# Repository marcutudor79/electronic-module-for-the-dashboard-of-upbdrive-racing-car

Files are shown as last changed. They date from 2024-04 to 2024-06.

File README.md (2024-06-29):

# ETTI-Bachelor's degree Applied Electronics


My Bachelor's degree that consists in research & design the following components:
- dashboard PCB with ESP32 SoC
- Test module PCB with Raspberry Pi Pico devboard
- Firmware for the ESP32 with ESP-IDF
- Firmware for the Raspberry Pi Pico with pico-sdk

# Thesis
The document can be referred [here.](Documentation/Thesis.pdf)

# Thesis summary
The thesis sumarry can be referred [here.](Documentation/Summary.pdf)

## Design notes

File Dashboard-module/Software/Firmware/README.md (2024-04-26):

# Firmware documentation

## Project structure:
```
- Firmware /
            - CMakeLists.txt /* project wide CMake */

            - components/ - 4dsystems-project/ - 4dsys.4dGenie /* the project from 4D
                                                                  Workshop IDE */
                          - esp32-arduino /* the arduino interface for ESP, used for
                                             compatibility between visi-genie and the
                                             ESP-IDF build system */
                          - visi-genie /* the interface for display communication */

            - main/       - CMakeLists.txt /* main CMakeLists, used to include the main.c */
                          - main.cpp       /* the main file of the project */

            - misc/         /* photos included in the README.md file */

            - README.md     /* project README file */
```

# How to run this project:
Install the SDK:
1. Go to VS Code tutorial for ESP-IDF extension from [here](https://github.com/espressif/vscode-esp-idf-extension/blob/master/docs/tutorial/install.md)
2. Install the ESP-IDF using the "EXPRESS" setup
3. The project was made by using the release version 5.1.1

Install the 4DSystems IDE:
1. Go to the 4DSystems website from [here](https://4dsystems.com.au/software/)
2. Download the free version of Workshop4 IDE
3. Open the file components/4dsystems-project/4dsys.4DGenie with Workshop4 IDE
4. Extract the SDCard from the display and connect it to your computer
5. Click on the project tab and set the Destination, Initial Form, Comms Speed, Comms and File System as in the picture below



6. Click on the home tab and then click on the Build (Copy/Load) button
7. A window will pop up, there you need to select the drive, that being the SDCard
from the display

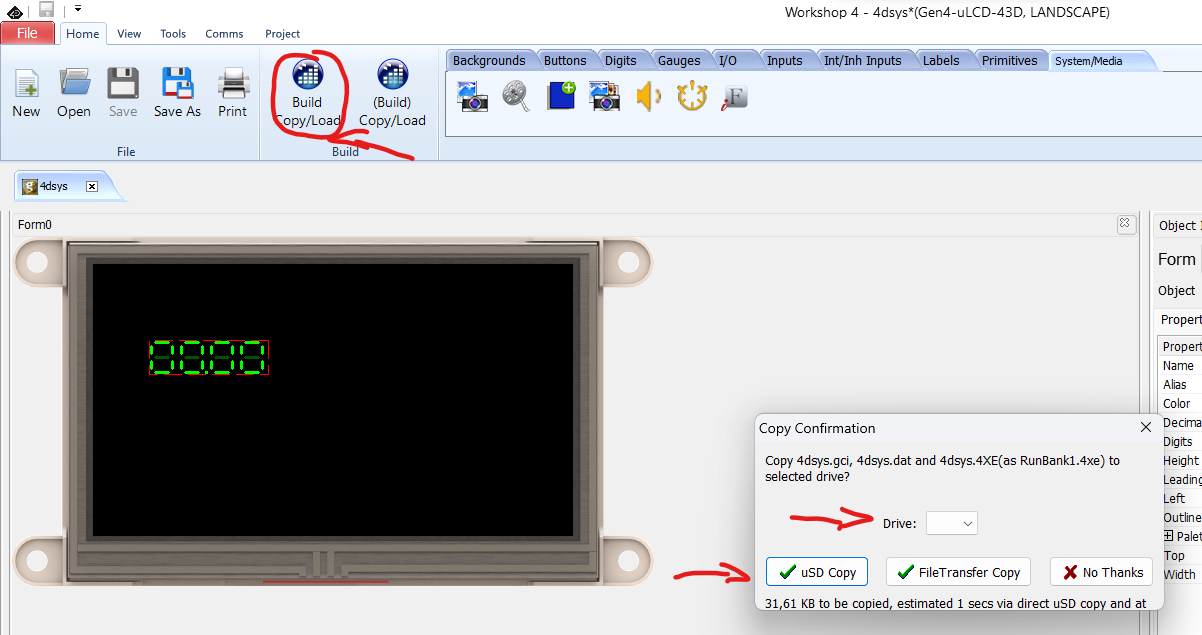
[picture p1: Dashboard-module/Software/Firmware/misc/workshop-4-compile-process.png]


8. Then select uSD Copy
9. After that, pop the SDCard back inside the screen
10. After a power cycle, it will prompt the message "flashing complete"
11. Now the display programming is complete

Run the project:
1. Open this directory "Firmware" in VS Code
2. Build the project by using ESP-IDF Build Project button
3. Select the COM port to your board
4. Flash the project by using UART
5. Enjoy the endless loop of numbers incrementing on the screen!

Schematic:
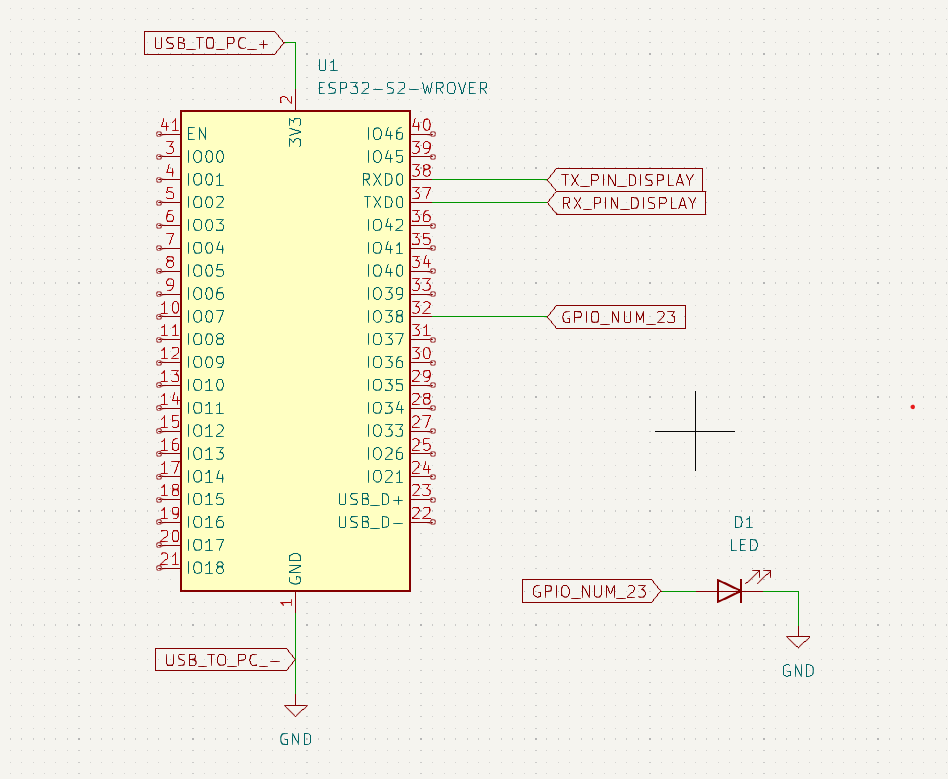
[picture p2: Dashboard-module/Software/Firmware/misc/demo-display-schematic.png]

NOTE: You will also need a 5V power supply in order to power up the display.

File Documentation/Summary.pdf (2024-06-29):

Study program: Applied Electronics (ETC-ELAeng), 2024

### Electronic Module for the Dashboard of a Formula Student Racing Car

Project objectives: The student must build from scratch an electronic module that will act as an interface between the pilot and the Formula Student race car it. The module will monitor the CAN bus of the car, from which it takes the following data points: oil temperature and water temperature, the status of the hybrid system as well as real-time data such: RPM and the current gear. It will also include an accelerometer on the same PCB. All the sampled data will be shown on an LCD module as well as a web interface which will be served by the HTTP server of the ESP32 microcontroller. The PCB will integrate an SD card that stores the data points in a file, which can be downloaded via the web interface.
A test module will be implemented on a second PCB for the student to showcase the functionality of the dashboard electronic module. It emulates the ECU of the Formula Student race car and will send via CAN the above-mentioned data. This module will feature the Raspberry Pi Pico microcontroller.
From a hardware perspective, the following components will be used:
- ESP32 WROOM 32 microcontroller as the brains of the dashboard electronic module
- SN65HVD230D CAN Transceiver that will act as an interface between ESP32 and the CAN bus
- LCD module from 4DSystems to show the data in a graphical interface to the pilot
- NeoPixel Stick - 8 x 5050 RGB LED that will be the shift bar, which signals the right moment to change the gear
- Panel mount buttons which will be the way of interacting with the dashboard module Project fulfilment and results: To fulfill the above-mentioned requirements, PCB Design as well as advanced C/C++ programming techniques had to be used. The contributions for this project are not trivial, since the PCB of the dashboard had to be designed from scratch, as well as the PCB of the testing module. No development boards were used on the dashboard module. It has a schematic that integrates all the needed peripherals as well as the ESP32 SoC with its necessary programming peripherals. To achieve this, the schematic of the ESP32 WROOM 32 dev board was analyzed and reimplemented in the KiCAD EDA.
Besides this, the dashboard includes standalone power delivery circuitry, which includes a LDO regulator, that converts the 5V power rail into a 3V3 power rail which is used for the ESP32, SD card module, CP2102 programming chip, the Hybrid selector, and the CAN transceiver SN65HVD230DR. The 5V rail is converted from the 12V power rail of the Formula Student racing car, by a buck converter. The circuit of the buck includes the components used in the reference design, given by its datasheet, for a 5V 3A output.
Other circuitry that needed to be implemented on the PCB were the MPU6050 accelerometer circuitry and the I2C lines that go to the ESP32 SoC, the SD card circuitry with all the necessary pull-up resistors as well as filtering for the 3V3 rail via ceramic capacitors of 1uF and 0.1uF. A lot of capacitors are used for filtering in the dashboard schematic to remove the noise induced by the buck. As a fail-over technique, the 3V3 rail can be supplied also by the LCD, which includes an LDO itself. This is achieved by placing on the PCB a solder jumper.
The LCD connector is a 30-pin ribbon cable connector. The pins of this connector were used as per the specification sheet of the 4DSystems company. Therefore, multiple LCD screens can be used with the same PCB as they all respect the same pinout of the ribbon connector.
The PCB is a 2 layer one, components being installed mostly on the front copper layer, the only exceptions being the LDO, because of its large footprint, and the automotive harness connector of the dashboard module, which needs to be oriented to the back of the PCB.

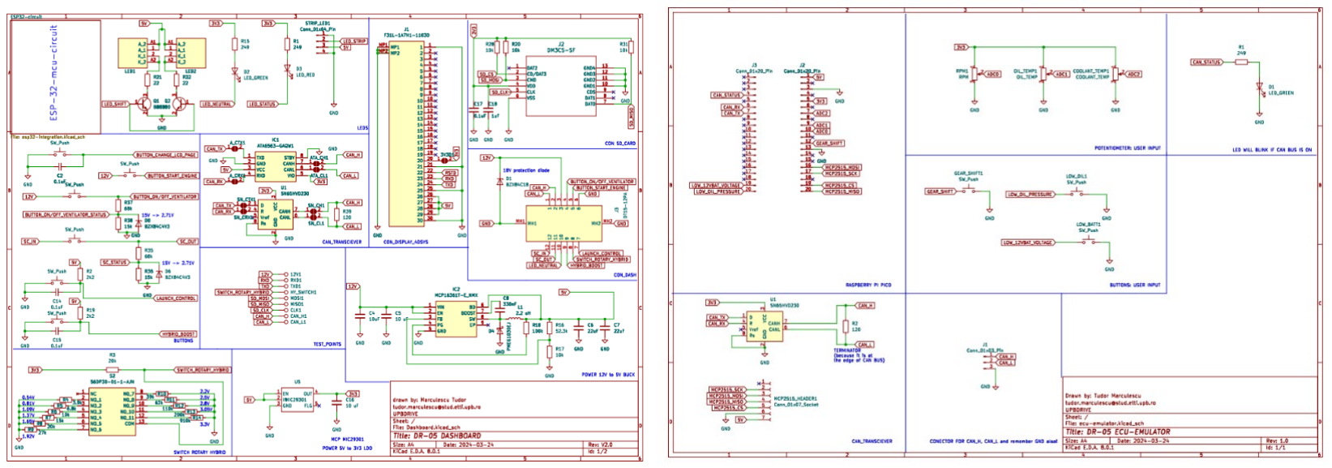
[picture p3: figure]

Fig. 1 Schematics of the dashboard module and test module
The PCB design of the test module is also based on a 2-layer approach, this time by using the PCB as an interconnection method between the Raspberry Pi Pico development board and the MCP2515 development board from Microchip, which includes a CAN controller that communicates via SPI with the Pico.
The PCB features 3 potentiometers that are used to emulate the RPM, water temperature and oil temperature signals from the ECU (Electronic Control Module), as well as 3 buttons that emulate a gear change, low oil pressure signal and low battery voltage signal. The low oil and low battery signals are used to showcase the function of the dashboard to display error messages on the LCD, in order to inform the pilot in case of catastrophic failures. The dashboard module and the test module will be connected via the CAN bus lines: CAN HIGH and CAN LOW, through which the test module will send CAN packets with the data acquired from the potentiometers and the buttons.

Do not think that this data is not converted into actual RPM and temperature values! Pico does all the data conversion in its firmware then formats the data into CAN packets which are send via the bus by the MCP2515 CAN controller.

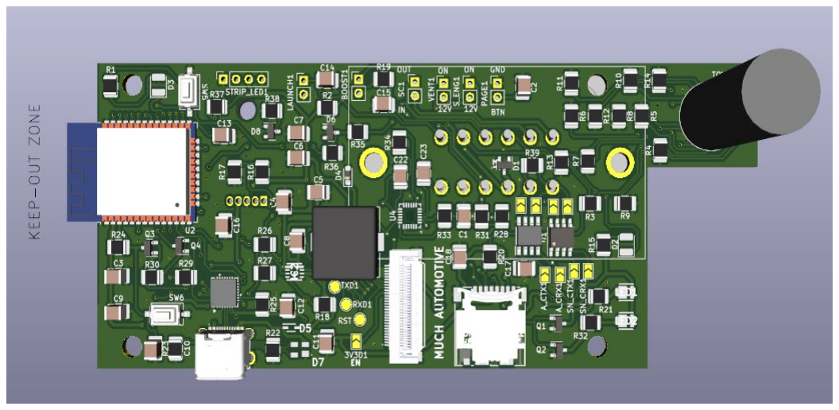
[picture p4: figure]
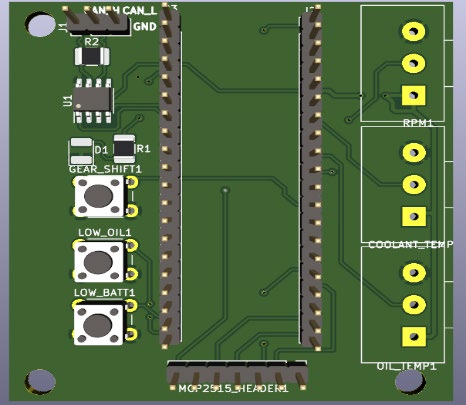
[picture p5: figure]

Fig. 2 3D View of the dashboard and test module
From a software point of view, the ESP32 one is complex, since it integrates a RTOS (Real Time Operating System). This allows the firmware to run on multiple threads on the same core of the microcontroller, and to also run parts of the firmware in parallel, by using multicore processing. In this way, CAN read and send tasks and LCD communication task, which are considered high priority, can be run completely parallel on 2 cores of the ESP32.
To achieve the highest performance possible, ESP32 was clocked to 240Mhz, which is the maximum supported by its Tensilica xTensa cores. Please note that this module is powered by a combustion engine, therefore efficiency is not considered, since it’s already lost in combustion. Espressif, the company which designed the ESP32 microcontroller, offers an IDF (Integrated Development Framework), written in C programming language, that includes a special flavor of FreeRTOS. It was adapted to run precisely on the hardware of Espressif. FreeRTOS is a renowned software solution for real-time applications in the automotive industry. If one uses this RTOS, he needs to break the code into multiple functions, which are called tasks.
Tasks are one of the most important concept of RTOS. They have different priorities, therefore when a high priority task is scheduled to be executed, it will preempt the lower priority ones. This allows the programmer to have certainty that high priority code will always be executed as scheduled by him. However, if no higher priority tasks need to be executed, lower priority ones are put into execution, therefore achieving the principle of multiple thread processing, since on one core, not only the high priority task is executed, assuming it will have some idle time, but also the lower priority ones. Multiple tasks had to be developed in order to achieve all the features proposed: accelerometer read task via I2C bus, SD card write task via SPI and VFS (Virtual File System) library, LCD communication task via UART2 IP, the HTTP server backend, etc. The html web interface was embedded in the binary that is flashed on the ESP32, therefore only the log file is stored on the SD card, not the index.html and its additional files used on the web interface.

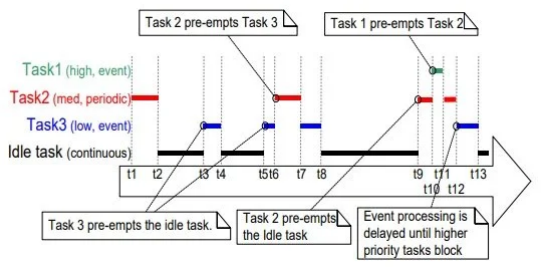
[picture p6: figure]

Fig. 3 Preemptive scheduling
To communicate with the NeoPixel LED bar, NRZ (Non-Return to Zero) protocol was used. The protocol was emulated with the RMT (ReMoTe control) library of the ESP32. The RMT is usually used to emulate TV remote control signals on the microcontroller’s pins, however, it can be also integrated to respect the protocol used by all 8 LEDs of the shift bar, which communicate with the ESP32 only via 1 pin. Data sharing between cores and threads is done using Semaphores which are a way of excluding race conditions on the same memory location.
Raspberry Pi Pico was programmed using bare metal programming techniques in C++. It does not include any operating system, and only runs one thread of monolithic code. This proves to be problematic, in case the code will get as complex as the dashboard firmware, but for the test board use case, it’s more than reasonable to not use RTOS. The main features are ADC reading of multiple potentiometers via ADC pins on the Pico development board and button state polling, the formatting of CAN packets. The packets are objects in C++, defined by a library developed for the MCP2515. In the dashboard firmware a common C data structure was used to store the display data, which is also integrated into the Pico C++ firmware to make the codebase more uniform and easier to understand. The CAN packet identifiers are also uniform between the dashboard and test module firmware as well as the packet formatting functions.

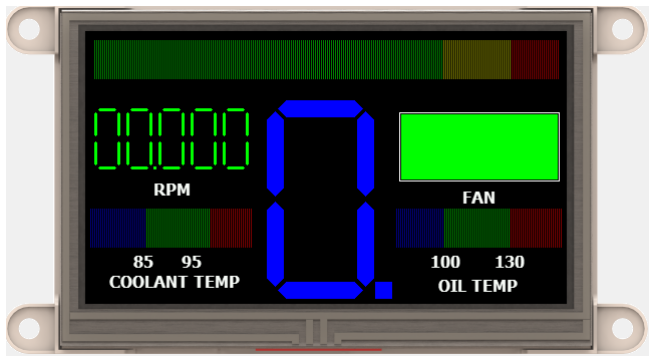
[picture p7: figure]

Fig. 4 Pilot interface
The dashboard was tested in an empiric method by trying all its functionalities and running it over an extended period. No crashes were detected during the test run time, therefore, it can be said that all the proposed student contributions were achieved, and the project development was a success.

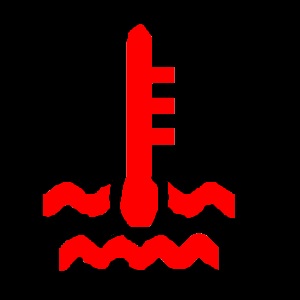
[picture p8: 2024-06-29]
Dashboard-module/Software/Firmware/4dsystems-project/high-water-temp.jpg

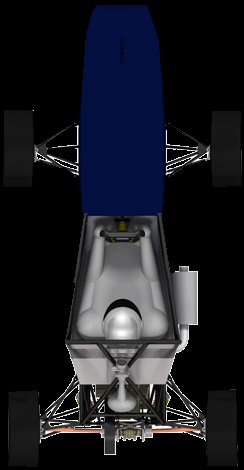
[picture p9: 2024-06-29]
Dashboard-module/Software/Firmware/4dsystems-project/4dsys.ImgData/car-tyrepressure.jpg

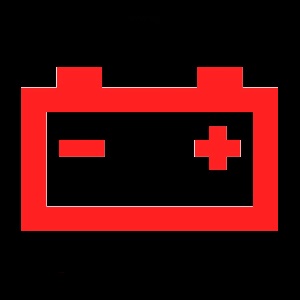
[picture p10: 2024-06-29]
Dashboard-module/Software/Firmware/4dsystems-project/low-battery.jpg

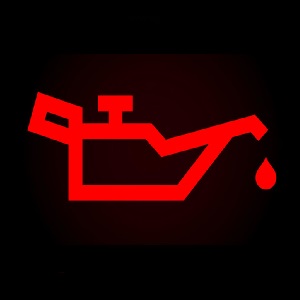
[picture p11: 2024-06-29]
Dashboard-module/Software/Firmware/4dsystems-project/4dsys.ImgData/low-oil-pressure.jpg

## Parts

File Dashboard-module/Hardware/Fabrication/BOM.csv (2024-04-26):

Reference | Value | Mouser Price/Stock | Qty
3V3 | TestPoint |  | 1
3V3D1 | SolderJumper_2_Open |  | 1
12V1 | TestPoint |  | 1
ATA_CH1 | SolderJumper_2_Open |  | 1
ATA_CL1 | SolderJumper_2_Open |  | 1
A_CRX1 | SolderJumper_2_Open |  | 1
A_CTX1 | SolderJumper_2_Open |  | 1
BOOST1 | SW_Push |  | 1
BOOT1 | TestPoint |  | 1
C1, C2, C9, C10, C12-C15, C17, C23 | 0.1uF | https://ro.mouser.com/ProductDetail/KEMET/C1210C104K5RACAUTO?qs=6HsNZxDn%2FfKYeoMwfZiUQw%3D%3D | 10
C3, C6, C7 | 22uF | https://www.mouser.co.uk/ProductDetail/Samsung-Electro-Mechanics/CL32B226KAJNNNE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 | 3
C4 | 10uF | https://www.mouser.co.uk/ProductDetail/Samsung-Electro-Mechanics/CL32B106KBJNNNE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 | 1
C5, C16 | 10 uF | https://www.mouser.co.uk/ProductDetail/Samsung-Electro-Mechanics/CL32B106KBJNNNE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 | 2
C8 | 330nF | https://ro.mouser.com/ProductDetail/KEMET/C1210C334J3RACTU?qs=6mECUfS0Ke6nQoOxT4SD9w%3D%3D | 1
C11, C18 | 1uF | https://ro.mouser.com/ProductDetail/KEMET/C1210C105K5RACAUTO?qs=6HsNZxDn%2FfKtobC7oxYdSw%3D%3D | 2
C22 | 2.2nF | https://ro.mouser.com/ProductDetail/KEMET/C1210C222KGRACAUTO?qs=YCa%2FAAYMW00YYMxRYUmDPg%3D%3D | 1
CAN_H1 | TestPoint |  | 1
CAN_L1 | TestPoint |  | 1
CLK1 | TestPoint |  | 1
D1 | BZX84C18 | https://eu.mouser.com/ProductDetail/Diotec-Semiconductor/BZX84C18?qs=OlC7AqGiEDmBdo82ioIQJw%3D%3D | 1
D2 | LED_GREEN | https://www.mouser.co.uk/ProductDetail/Broadcom-Avago/ASMT-BG20-AS000?qs=ZNK0BnemlqFrc3sIHSfGyw%3D%3D | 1
D3 | LED_RED | https://www.mouser.co.uk/ProductDetail/Broadcom-Avago/ASMT-BR20-AS000?qs=ZNK0BnemlqE0pAy34cXyOA%3D%3D | 1
D4 | PMEG1030EJ | https:/ro.mouser.com/ProductDetail/Nexperia/PMEG1030EJ115?qs=LOCUfHb8d9vmk7P%2FuYbs5A%3D%3D | 1
D5 | BAT760-7 | https://www.mouser.co.uk/ProductDetail/Diodes-Incorporated/BAT760-7?qs=JV7lzlMm3yKDDyO09xoRbQ%3D%3D | 1
D6, D8 | BZX84C4V3 | https://eu.mouser.com/ProductDetail/Diotec-Semiconductor/BZX84C18?qs=OlC7AqGiEDmBdo82ioIQJw%3D%3D | 2
D7 | SP0503BAHTG | https://www.mouser.co.uk/ProductDetail/Littelfuse/SP0503BAHTG?qs=uD%2FdkN7XIa0NTYXwHdELYA%3D%3D | 1
EN1 | TestPoint |  | 1
GND1 | TestPoint |  | 1
HY_SWITCH1 | TestPoint |  | 1
IC1 | ATA6563-GAQW1 | https://www.mouser.co.uk/ProductDetail/Microchip-Technology/ATA6563-GAQW1?qs=byeeYqUIh0Or75RXPLSWhg%3D%3D | 1
IC2 | MCP16361T-E_NMX | https://www.mouser.co.uk/ProductDetail/Microchip-Technology/MCP16361T-E-NMX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 | 1
J1 | F31L-1A7H1-11030 | https://www.mouser.co.uk/ProductDetail/Amphenol-Aorora/F31L-1A7H1-11030?qs=xZ%2FP%252Ba9zWqba3JhFjnTbQA%3D%3D | 1
J2 | DM3CS-SF | https://eu.mouser.com/ProductDetail/Hirose-Connector/DM3CS-SF?qs=tTj%252BmQ3KZwbB9K5zh89Rcw%3D%3D | 1
J3 | DT15-12PA | https://www.mouser.co.uk/ProductDetail/TE-Connectivity-DEUTSCH/DT15-12PA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 | 1
J6 | USB4800-03-A | https://www.mouser.co.uk/ProductDetail/GCT/USB4800-03-A?qs=vvQtp7zwQdMkfG8vViEZoQ%3D%3D | 1
L1 | 2.2 uH | https://www.mouser.co.uk/ProductDetail/Vishay-Dale/IHLP5050CEER2R2M01?qs=rJUnqL1uSaJB3797G0edMw%3D%3D | 1
LAUNCH1 | SW_Push |  | 1
LED1, LED2 | GR_PSLM31.23-FTGP-45-FG | https://www.mouser.co.uk/ProductDetail/OSRAM-Opto-Semiconductors/GR-PSLM3123-FTGP-45-FG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 | 2
MISO1 | TestPoint |  | 1
MOSI1 | TestPoint |  | 1
PAGE1 | SW_Push |  | 1
Q1-Q4 | BC850 | https://www.mouser.co.uk/ProductDetail/Infineon-Technologies/BC-850B-E6327?qs=OWKQh20churjjEOHOyP6%2FA%3D%3D | 4
R1, R15 | 249 | https://www.mouser.co.uk/ProductDetail/YAGEO/AC1210FR-07249RL?qs=9h0bZHM%2F3zLfUZmwuLVpmw%3D%3D | 2
R2, R19 | 2k2 | https://www.mouser.co.uk/ProductDetail/YAGEO/RC1210JR-072K2L?qs=6sj9KdP9svikZPTMueIMVw%3D%3D | 2
R3, R8 | 20k | https://www.mouser.co.uk/c/passive-components/resistors/film-resistors/thick-film-resistors-smd/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 | 2
R4 | 3.9k | https://www.mouser.co.uk/ProductDetail/YAGEO/AC1210FR-073K9L | 1
R5 | 6.8k | https://www.mouser.co.uk/ProductDetail/YAGEO/AC1210JR-076K8L?qs=tggtontpCXOplOrJrmjEFg%3D%3D | 1
R6, R17, R20, R28, R31 | 10k | -- mixed values -- | 5
R7, R36, R38 | 15k | -- mixed values -- | 3
R9 | 27k | https://www.mouser.co.uk/ProductDetail/YAGEO/RC1210JR-0727KL?qs=6sj9KdP9svjllLJjfo7WyQ%3D%3D | 1
R10 | 39k | https://www.mouser.co.uk/ProductDetail/YAGEO/AC1210FR-0739KL?qs=tggtontpCXMMf8qT%2FAbRXA%3D%3D | 1
R11 | 62k | https://www.mouser.co.uk/ProductDetail/YAGEO/RC1210FR-0762KL?qs=H6bTqIa4pvXpTu6n%252B%2FNlGA%3D%3D | 1
R12 | 110k | https://www.mouser.co.uk/ProductDetail/YAGEO/RC1210FR-07110KL?qs=H6bTqIa4pvVTUx5WugF8mg%3D%3D | 1
R13 | 200k | https://www.mouser.co.uk/ProductDetail/YAGEO/RC1210JR-07200KL?qs=CteSnpDdeuDthvIZoegoUw%3D%3D | 1
R14 | 910k | https://www.mouser.co.uk/c/passive-components/resistors/film-resistors/thick-film-resistors-smd/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 | 1
R16 | 52.3k | https://ro.mouser.com/ProductDetail/Panasonic/ERJ-14NF5232U?qs=nho8PGNfA6qGgoBnQlUYNQ%3D%3D | 1
R18 | 100k | https://ro.mouser.com/c/?q=RC1210FR-07100KL | 1
R21, R32 | 22 | https://www.mouser.co.uk/ProductDetail/YAGEO/AC1210JR-0722RL?qs=9h0bZHM%2F3zJh6BccmgJFgA%3D%3D | 2
R22, R23 | 5.1k | https://www.mouser.co.uk/ProductDetail/YAGEO/RC1210FR-075K1L?qs=H6bTqIa4pvX6KFbI5%252BKNQQ%3D%3D | 2
R24, R25, R29, R30 | 10K | https://ro.mouser.com/ProductDetail/SEI-Stackpole/RMCF1210FT10K0?qs=FESYatJ8odLSM832du%2FSXw%3D%3D | 4
R26 | 22.1k | https://ro.mouser.com/ProductDetail/Vishay-Dale/CRCW121022K1FKEA?qs=grCzdrupEeFjmAghhFVXQQ%3D%3D | 1
R27 | 47.5k | https://ro.mouser.com/ProductDetail/Vishay-Dale/CRCW121047K5FKEA | 1
R33, R34 | 1.5k | https://www.mouser.co.uk/ProductDetail/YAGEO/RC1210JR-071K5L?qs=6sj9KdP9sviSuJXf5F9TBg%3D%3D | 2
R35, R37 | 68k | -- mixed values -- | 2
R39 | 120 | https://www.mouser.co.uk/ProductDetail/YAGEO/RC1210JR-13120RL?qs=qpJ%252B%252B%252Bdg6p3wDlUWdPJ5VQ%3D%3D | 1
RXD0, RXD1 | TestPoint |  | 2
S2 | 56DP30-01-1-AJN | https://www.mouser.co.uk/ProductDetail/Grayhill/56DP30-01-1-AJN?qs=ls7QRyWmRk4hkEWp7Raugg%3D%3D | 1
SC1 | SW_Push |  | 1
SCL1 | TestPoint |  | 1
SDA1 | TestPoint |  | 1
SN_CH1 | SolderJumper_2_Open |  | 1
SN_CL1 | SolderJumper_2_Open |  | 1
SN_CRX1 | SolderJumper_2_Open |  | 1
SN_CTX1 | SolderJumper_2_Open |  | 1
STRIP_LED1 | Conn_01x04_Pin | https://www.mouser.co.uk/ProductDetail/Harwin/M20-9992046?qs=%252Bk6%2F5FB6qrkVgm0dNoxueg%3D%3D | 1
SW5, SW6 | boot_button | https://ro.mouser.com/ProductDetail/CK/PTS636-SK25-SMTR-LFS?qs=vLWxofP3U2wQKecmu1U%2FMA%3D%3D | 2
S_ENG1 | SW_Push |  | 1
TXD0, TXD1 | TestPoint |  | 2
U1 | SN65HVD230 | https://eu.mouser.com/ProductDetail/Texas-Instruments/SN65HVD230DR?qs=QViXGNcIEAtifeQR3pYVUQ%3D%3D | 1
U2 | ESP32-WROOM-32 | https://ro.mouser.com/ProductDetail/Espressif-Systems/ESP32-WROOM-32E-H4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 | 1
U3 | CP2102-GMR | https://ro.mouser.com/ProductDetail/Silicon-Labs/CP2102-GMR?qs=cNyzPCcHMUWu%2FiPhR8KQAw%3D%3D | 1
U4 | MPU-6050 | https://www.mouser.co.uk/ProductDetail/TDK-InvenSense/MPU-6050?qs=u4fy%2FsgLU9O14B5JgyQFvg%3D%3D | 1
U5 | MIC29301 |  | 1
VENT1 | SW_Push |  | 1

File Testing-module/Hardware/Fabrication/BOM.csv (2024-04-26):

Reference | Value | Mouser Price/Stock | Qty
COOLANT_TEMP1 | COOLANT_TEMP | https://eu.mouser.com/ProductDetail/CUI-Devices/PTN16-A50115K1B1?qs=VJzv269c%252BPYgMEvZAio5MQ%3D%3D | 1
D1 | LED_GREEN | https://www.mouser.co.uk/ProductDetail/Broadcom-Avago/ASMT-BG20-AS000?qs=ZNK0BnemlqFrc3sIHSfGyw%3D%3D | 1
GEAR_SHIFT1 | SW_Push | https://eu.mouser.com/ProductDetail/CUI-Devices/TS02-66-73-BK-160-LCR-D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 | 1
J1 | Conn_01x03_Pin | https://www.mouser.co.uk/ProductDetail/Harwin/M20-9992046?qs=%252Bk6%2F5FB6qrkVgm0dNoxueg%3D%3D | 1
J2, J3 | Conn_01x20_Pin | https://www.mouser.co.uk/ProductDetail/Harwin/M20-9992046?qs=%252Bk6%2F5FB6qrkVgm0dNoxueg%3D%3D | 2
LOW_BATT1 | SW_Push | https://eu.mouser.com/ProductDetail/CUI-Devices/TS02-66-73-BK-160-LCR-D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 | 1
LOW_OIL1 | SW_Push | https://eu.mouser.com/ProductDetail/CUI-Devices/TS02-66-73-BK-160-LCR-D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 | 1
MCP2515_HEADER1 | Conn_01x07_Socket | https://www.mouser.co.uk/ProductDetail/Harwin/M20-9992046?qs=%252Bk6%2F5FB6qrkVgm0dNoxueg%3D%3D | 1
OIL_TEMP1 | OIL_TEMP | https://eu.mouser.com/ProductDetail/CUI-Devices/PTN16-A50115K1B1?qs=VJzv269c%252BPYgMEvZAio5MQ%3D%3D | 1
R1 | 249 | https://www.mouser.co.uk/ProductDetail/YAGEO/AC1210FR-07249RL?qs=9h0bZHM%2F3zLfUZmwuLVpmw%3D%3D | 1
R2 | 120 | https://www.mouser.co.uk/ProductDetail/YAGEO/RC1210JR-13120RL?qs=qpJ%252B%252B%252Bdg6p3wDlUWdPJ5VQ%3D%3D | 1
RPM1 | RPM | https://eu.mouser.com/ProductDetail/CUI-Devices/PTN16-A50115K1B1?qs=VJzv269c%252BPYgMEvZAio5MQ%3D%3D | 1
U1 | SN65HVD230 | https://eu.mouser.com/ProductDetail/Texas-Instruments/SN65HVD230DR?qs=QViXGNcIEAtifeQR3pYVUQ%3D%3D | 1

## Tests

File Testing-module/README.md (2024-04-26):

# ECU Emulator

## Description
In order to debug the CAN bus as well as the dashboard module, this ECU Emulator
injects CAN packets into the CAN bus. It is a replacement for the ECU itself, because
we cannot use it just for electronics debugging, it has to be mounted in the FS car.

## How does it work
This ECU Emulator uses a potentiometer to emulate the accelerator pedal of the FS car
as well as a button to emulate the gear shift. The potentiometer is read via the built-in
ADC module of the Raspberry Pi Pico board, and the button is read using GPIO functions.

### How is the data generated
- rpm is generated using a constant 800 + the potentiometer value + a random number
between 0 - 49 in order to emulate the actual rpm of the FS car. The expected range is
between 800 - 13000.
- current gear is initially 0 (netural) and incremented when the button is pressed, until 4,
then it is set back to 0.
- all the other data is assigned the saw tooth signal between 0 - 250.

The CAN packets are formatted with respect to the CAN Packet allocation excel and then sent via the CAN bus.

## Project structure
```
- Docs     /* folder the documentation files */
- Firmware /
            - components/ - adc                 /* part of the code that enables the onboard
                                                    adc and configures a gpio to read a button */
                          - can                 /* part of the code that enables can communication
                                                    via the can bus transciever
                                                    also formats the packets according to the CAN
                                                    packet allocation */
                          - common              /* contains a header file in which the pins used
                                                    in the project are defined */
                          - heartbeat           /* part of the code that enables the built-in LED
                                                    to blink, for debug purposes */
                          - signal-generation   /* part of the code that generates the rpm data,
                                                   CurrentGear data and a sawtooth signal that
                                                   will replace the other data in the CAN packets */
            - main                /* contains the main source and header file with
                                    which describes the main loop of the program */
            - modules             /* contains can2040 git submodule that enables
                                     the PICO to communicate via CAN using bit banging
                                     on GPIOs */

- README.md /* project README file */
```

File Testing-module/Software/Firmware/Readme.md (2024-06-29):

# ECU Emulator Firmware

## How to build the project (on Windows)
1. Open a console (cmd) with the path set to 'Firmware' directory

2. Change directory into the 'main' folder

    ```
    cd main
    ```

3. Create a build directory

    ```
    mkdir build
    cd build
    ```

4. Use 'cmake' to generate the build files
    ```
    cmake ..
    ```

5. Build the project using 'cmake'
    ```
    cmake --build .
    ```

6. Copy main.uf2 file on the Raspberry Pi Pico board

## Prerequisites (on Windows)

Follow this tutorial [https://shawnhymel.com/2096/how-to-set-up-raspberry-pi-pico-c-c-toolchain-on-windows-with-vs-code/.](https://shawnhymel.com/2096/how-to-set-up-raspberry-pi-pico-c-c-toolchain-on-windows-with-vs-code/)

! 'Download Pico SDK and Examples' part is not needed for this project

! 'Install VS Code' part is not needed for this project

! 'Build Blink Example' part is needed for this project

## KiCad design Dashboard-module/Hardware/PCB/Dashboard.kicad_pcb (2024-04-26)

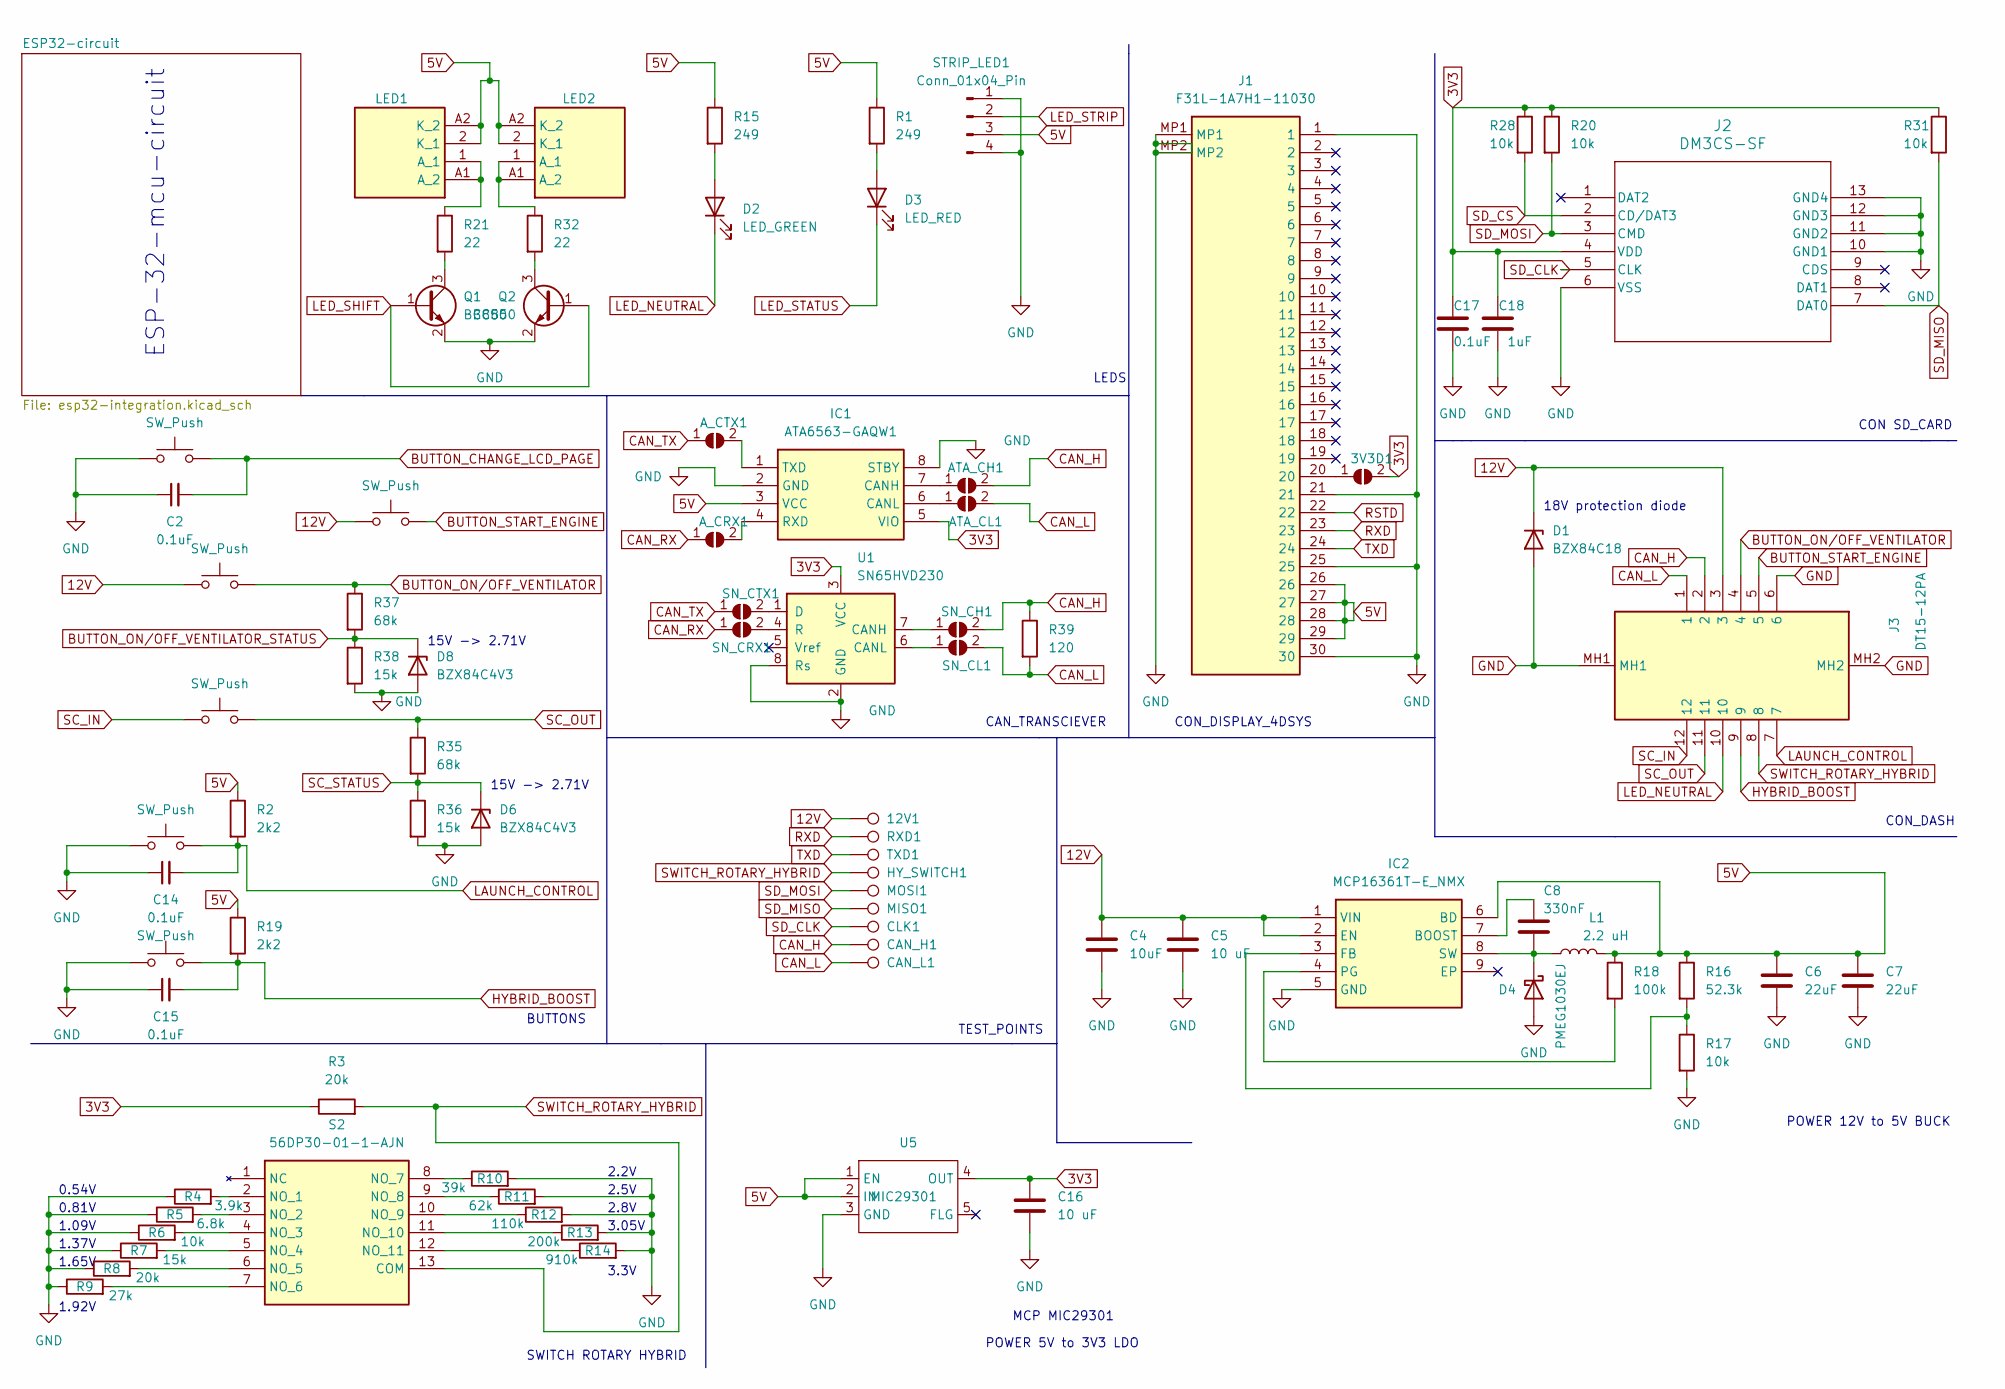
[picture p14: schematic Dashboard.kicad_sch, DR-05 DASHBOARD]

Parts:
3V3D1: SolderJumper_2_Open; SolderJumper-2_P1.3mm_Open_TrianglePad1.0x1.5mm
12V1: TestPoint; TestPoint_Pad_D2.0mm
ATA_CH1: SolderJumper_2_Open; SolderJumper-2_P1.3mm_Open_TrianglePad1.0x1.5mm
ATA_CL1: SolderJumper_2_Open; SolderJumper-2_P1.3mm_Open_TrianglePad1.0x1.5mm
A_CRX1: SolderJumper_2_Open; SolderJumper-2_P1.3mm_Open_TrianglePad1.0x1.5mm
A_CTX1: SolderJumper_2_Open; SolderJumper-2_P1.3mm_Open_TrianglePad1.0x1.5mm
BOOST1: SW_Push; PinHeader_1x02_P2.54mm_Vertical
C2, C14, C15, C17: 0.1uF; C_1210_3225Metric_Pad1.33x2.70mm_HandSolder
C4: 10uF; C_1210_3225Metric_Pad1.33x2.70mm_HandSolder
C5, C16: 10 uF; C_1210_3225Metric_Pad1.33x2.70mm_HandSolder
C6, C7: 22uF; C_1210_3225Metric_Pad1.33x2.70mm_HandSolder
C8: 330nF; C_1210_3225Metric_Pad1.33x2.70mm_HandSolder
C18: 1uF; C_1210_3225Metric_Pad1.33x2.70mm_HandSolder
CAN_H1: TestPoint; TestPoint_Pad_D2.0mm
CAN_L1: TestPoint; TestPoint_Pad_D2.0mm
CLK1: TestPoint; TestPoint_Pad_D2.0mm
D1: BZX84C18; SOT-23
D2: LED_GREEN; D_1210_3225Metric
D3: LED_RED; D_1210_3225Metric
D4: PMEG1030EJ; D_SOD-323_HandSoldering
D6, D8: BZX84C4V3; SOT-23
HY_SWITCH1: TestPoint; TestPoint_Pad_D2.0mm
IC1: ATA6563-GAQW1; SOIC127P600X175-8N; Mouser Part Number 579-ATA6563-GAQW1
IC2: MCP16361T-E_NMX; MCP16361TENMX; Mouser Part Number 579-MCP16361T-E/NMX
J1: F31L-1A7H1-11030; F31L1A7H111030; Mouser Part Number 649-F31L-1A7H1-11030
J2: DM3CS-SF; DM3CS_SF
J3: DT15-12PA; DT1512PA; Mouser Part Number 571-DT15-12PA
L1: 2.2 uH; L_Vishay_IHLP-5050
LAUNCH1: SW_Push; PinHeader_1x02_P2.54mm_Vertical
LED1, LED2: GR_PSLM31.23-FTGP-45-FG; GRPSLM3123FTGP45FG; Mouser Part Number 720-PSLM3123A4675
MISO1: TestPoint; TestPoint_Pad_D2.0mm
MOSI1: TestPoint; TestPoint_Pad_D2.0mm
PAGE1: SW_Push; PinHeader_1x02_P2.54mm_Vertical
Q1, Q2: BC850; SOT-23
R1, R15: 249; R_1210_3225Metric
R2, R19: 2k2; R_1210_3225Metric
R3, R8: 20k; R_1210_3225Metric_Pad1.30x2.65mm_HandSolder
R4: 3.9k; R_1210_3225Metric_Pad1.30x2.65mm_HandSolder
R5: 6.8k; R_1210_3225Metric_Pad1.30x2.65mm_HandSolder
R6, R17, R20, R28, R31: 10k; R_1210_3225Metric_Pad1.30x2.65mm_HandSolder
R7: 15k; R_1210_3225Metric_Pad1.30x2.65mm_HandSolder
R9: 27k; R_1210_3225Metric_Pad1.30x2.65mm_HandSolder
R10: 39k; R_1210_3225Metric_Pad1.30x2.65mm_HandSolder
R11: 62k; R_1210_3225Metric_Pad1.30x2.65mm_HandSolder
R12: 110k; R_1210_3225Metric_Pad1.30x2.65mm_HandSolder
R13: 200k; R_1210_3225Metric_Pad1.30x2.65mm_HandSolder
R14: 910k; R_1210_3225Metric_Pad1.30x2.65mm_HandSolder
R16: 52.3k; R_1210_3225Metric_Pad1.30x2.65mm_HandSolder
R18: 100k; R_1210_3225Metric_Pad1.30x2.65mm_HandSolder
R21, R32: 22; R_1210_3225Metric
R35, R37: 68k; R_1210_3225Metric
R36, R38: 15k; R_1210_3225Metric
R39: 120; R_1210_3225Metric_Pad1.30x2.65mm_HandSolder
RXD1: TestPoint; TestPoint_Pad_D2.0mm
S2: 56DP30-01-1-AJN; 56SP3001B12N; Mouser Part Number 706-56DP30-01-1-AJN
SC1: SW_Push; PinHeader_1x02_P2.54mm_Vertical
SN_CH1: SolderJumper_2_Open; SolderJumper-2_P1.3mm_Open_TrianglePad1.0x1.5mm
SN_CL1: SolderJumper_2_Open; SolderJumper-2_P1.3mm_Open_TrianglePad1.0x1.5mm
SN_CRX1: SolderJumper_2_Open; SolderJumper-2_P1.3mm_Open_TrianglePad1.0x1.5mm
SN_CTX1: SolderJumper_2_Open; SolderJumper-2_P1.3mm_Open_TrianglePad1.0x1.5mm
STRIP_LED1: Conn_01x04_Pin; PinSocket_1x04_P2.54mm_Vertical
S_ENG1: SW_Push; PinHeader_1x02_P2.54mm_Vertical
TXD1: TestPoint; TestPoint_Pad_D2.0mm
U1: SN65HVD230; SOIC-8_3.9x4.9mm_P1.27mm
U5: MIC29301; TO-220-5_Horizontal_TabDown
VENT1: SW_Push; PinHeader_1x02_P2.54mm_Vertical

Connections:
3V3: 3V3D1.2 (B), C16.1, C17.1, C18.1, IC1.5 (VIO), J2.4 (VDD), R3.1, R20.1, R28.1, R31.1, U1.3 (VCC), U5.4 (OUT); also elsewhere on the board
5V: C6.1, C7.1, IC1.3 (VCC), IC2.6 (BD), J1.26, J1.27, J1.28, J1.29, L1.2, LED1.2 (K_1), LED1.A2 (K_2), LED2.2 (K_1), LED2.A2 (K_2), R1.1, R2.1, R15.1, R16.1, R18.1, R19.1, STRIP_LED1.3, U5.1 (EN), U5.2 (IN); also elsewhere on the board
12V: 12V1.1, C4.1, C5.1, D1.3 (K), IC2.1 (VIN), IC2.2 (EN), J3.3, S_ENG1.2, VENT1.2
BUTTON_CHANGE_LCD_PAGE: C2.2, PAGE1.2; also elsewhere on the board
BUTTON_ON/OFF_VENTILATOR: J3.4, R37.1, VENT1.1
BUTTON_ON/OFF_VENTILATOR_STATUS: D8.3 (K), R37.2, R38.1; also elsewhere on the board
BUTTON_START_ENGINE: J3.5, S_ENG1.1
CAN_H: ATA_CH1.2 (B), CAN_H1.1, J3.2, R39.1, SN_CH1.2 (B)
CAN_L: ATA_CL1.2 (B), CAN_L1.1, J3.1, R39.2, SN_CL1.2 (B)
CAN_RX: A_CRX1.1 (A), SN_CRX1.1 (A); also elsewhere on the board
CAN_TX: A_CTX1.1 (A), SN_CTX1.1 (A); also elsewhere on the board
GND: BOOST1.2, C2.1, C4.2, C5.2, C6.2, C7.2, C14.1, C15.1, C16.2, C17.2, C18.2, D1.1 (A), D4.2 (A), D6.1 (A), D8.1 (A), IC1.2 (GND), IC1.8 (STBY), IC2.5 (GND), J1.1, J1.21, J1.25, J1.30, J1.MP1, J1.MP2, J2.6 (VSS), J2.10 (GND1), J2.11 (GND2), J2.12 (GND3), J2.13 (GND4), J3.6, J3.MH1, J3.MH2, LAUNCH1.2, PAGE1.1, Q1.2 (E), Q2.2 (E), R4.1, R5.1, R6.1, R7.1, R8.1, R9.1, R10.2, R11.2, R12.2, R13.2, R14.2, R17.2, R36.2, R38.2, STRIP_LED1.1, STRIP_LED1.4, U1.2 (GND), U1.8 (Rs), U5.3 (GND); also elsewhere on the board
HYBRID_BOOST: BOOST1.1, C15.2, J3.9, R19.2
LAUNCH_CONTROL: C14.2, J3.7, LAUNCH1.1, R2.2
LED_NEUTRAL: D2.1 (K), J3.10; also elsewhere on the board
LED_SHIFT: Q1.1 (B), Q2.1 (B); also elsewhere on the board
LED_STATUS: D3.1 (K); also elsewhere on the board
LED_STRIP: STRIP_LED1.2; also elsewhere on the board
unnamed: 3V3D1.1 (A), J1.20
unnamed: ATA_CH1.1 (A), IC1.7 (CANH)
unnamed: ATA_CL1.1 (A), IC1.6 (CANL)
unnamed: A_CRX1.2 (B), IC1.4 (RXD)
unnamed: A_CTX1.2 (B), IC1.1 (TXD)
unnamed: D2.2 (A), R15.2
unnamed: D3.2 (A), R1.2
unnamed: C8.2, D4.1 (K), IC2.8 (SW), L1.1
unnamed: C8.1, IC2.7 (BOOST)
unnamed: IC2.3 (FB), R16.2, R17.1
unnamed: IC2.4 (PG), R18.2
unnamed: LED1.1 (A_1), LED1.A1 (A_2), R21.1
unnamed: LED2.1 (A_1), LED2.A1 (A_2), R32.1
unnamed: Q1.3 (C), R21.2
unnamed: Q2.3 (C), R32.2
unnamed: R4.2, S2.2 (NO_1)
unnamed: R5.2, S2.3 (NO_2)
unnamed: R6.2, S2.4 (NO_3)
unnamed: R7.2, S2.5 (NO_4)
unnamed: R8.2, S2.6 (NO_5)
unnamed: R9.2, S2.7 (NO_6)
unnamed: R10.1, S2.8 (NO_7)
unnamed: R11.1, S2.9 (NO_8)
unnamed: R12.1, S2.10 (NO_9)
unnamed: R13.1, S2.11 (NO_10)
unnamed: R14.1, S2.12 (NO_11)
unnamed: SN_CH1.1 (A), U1.7 (CANH)
unnamed: SN_CL1.1 (A), U1.6 (CANL)
unnamed: SN_CRX1.2 (B), U1.4 (R)
unnamed: SN_CTX1.2 (B), U1.1 (D)
RSTD: J1.22; also elsewhere on the board
RXD: J1.23, RXD1.1; also elsewhere on the board
SC_IN: J3.12, SC1.2
SC_OUT: J3.11, R35.1, SC1.1
SC_STATUS: D6.3 (K), R35.2, R36.1; also elsewhere on the board
SD_CLK: CLK1.1, J2.5 (CLK); also elsewhere on the board
SD_CS: J2.2 (CD/DAT3), R28.2; also elsewhere on the board
SD_MISO: J2.7 (DAT0), MISO1.1, R31.2; also elsewhere on the board
SD_MOSI: J2.3 (CMD), MOSI1.1, R20.2; also elsewhere on the board
SWITCH_ROTARY_HYBRID: HY_SWITCH1.1, J3.8, R3.2, S2.13 (COM); also elsewhere on the board
TXD: J1.24, TXD1.1; also elsewhere on the board

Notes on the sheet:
2.2V
1.37V
BUTTONS
1.65V
TEST_POINTS
POWER 5V to 3V3 LDO
0.54V
CON SD_CARD
LEDS
3.3V
CON_DASH
CAN_TRANSCIEVER
15V -> 2.71V
0.81V
SWITCH ROTARY HYBRID
2.8V
CON_DISPLAY_4DSYS
1.92V
2.5V
1.09V
3.05V
ESP-32-mcu-circuit
POWER 12V to 5V BUCK
18V protection diode
MCP MIC29301

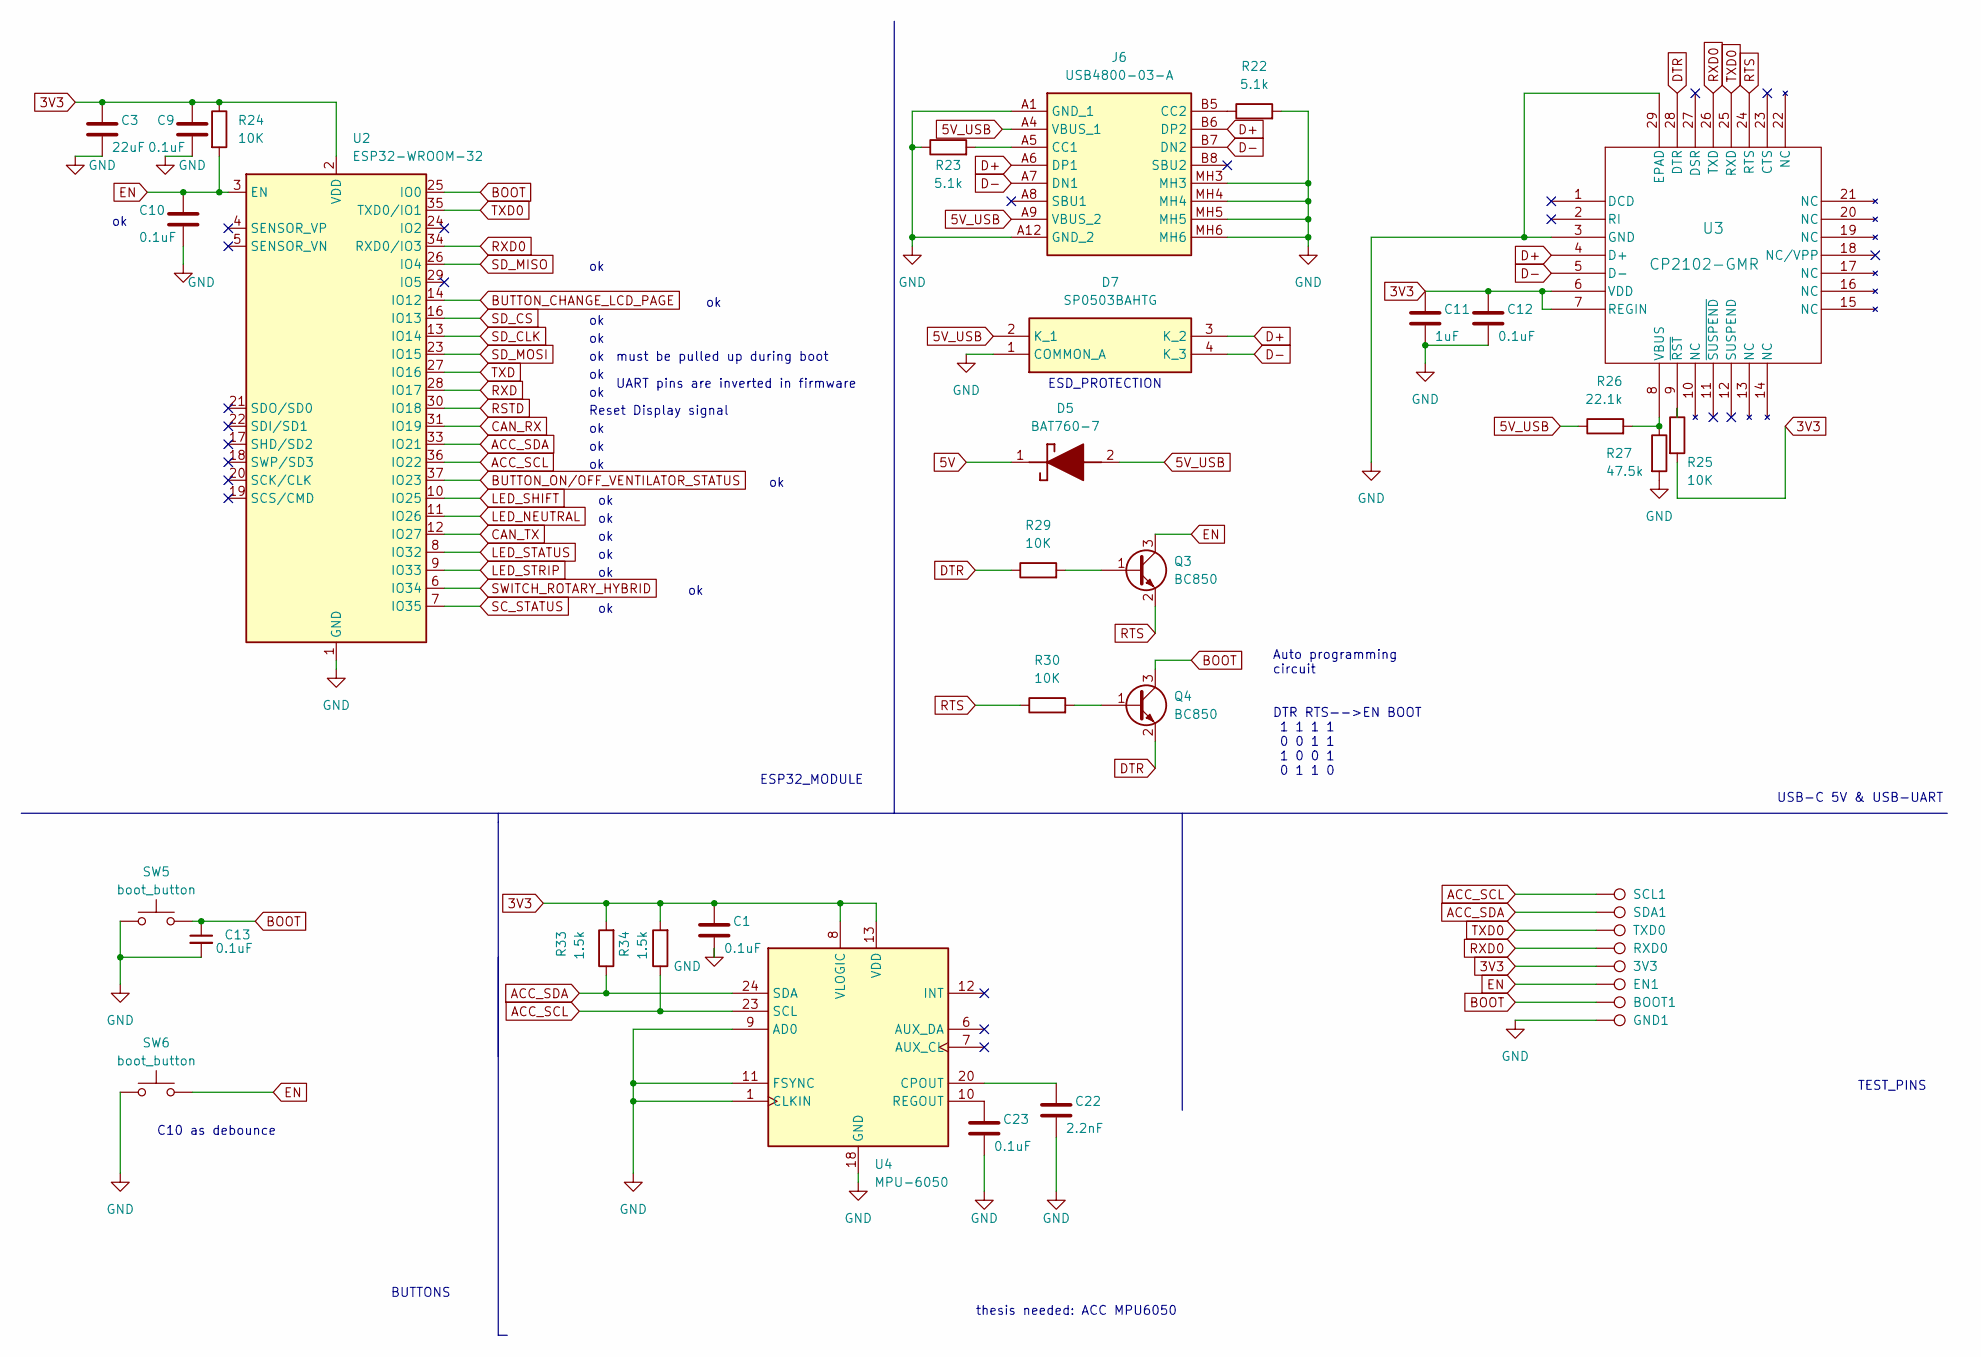
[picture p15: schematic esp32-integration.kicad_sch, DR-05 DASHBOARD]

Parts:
3V3: TestPoint; TestPoint_Pad_D2.0mm
BOOT1: TestPoint; TestPoint_Pad_D2.0mm
C1, C9, C10, C12, C23: 0.1uF; C_1210_3225Metric_Pad1.33x2.70mm_HandSolder
C3: 22uF; C_1210_3225Metric_Pad1.33x2.70mm_HandSolder
C11: 1uF; C_1210_3225Metric_Pad1.33x2.70mm_HandSolder
C13: 0.1uF; C_1210_3225Metric_Pad1.33x2.70mm_HandSolder; Manufacturer_Part_Number C1210C104K5RACAUTO
C22: 2.2nF; C_1210_3225Metric_Pad1.33x2.70mm_HandSolder
D5: BAT760-7; Mouser Part Number 621-BAT760-7
D7: SP0503BAHTG; Mouser Part Number 576-SP0503BAHTG
EN1: TestPoint; TestPoint_Pad_D2.0mm
GND1: TestPoint; TestPoint_Pad_D2.0mm
J6: USB4800-03-A; USB480003A; Mouser Part Number 640-USB4800-03-A
Q3, Q4: BC850; SOT-23
R22, R23: 5.1k; R_1210_3225Metric_Pad1.30x2.65mm_HandSolder
R24, R25, R29, R30: 10K; R_1210_3225Metric_Pad1.30x2.65mm_HandSolder
R26: 22.1k; R_1210_3225Metric_Pad1.30x2.65mm_HandSolder
R27: 47.5k; R_1210_3225Metric_Pad1.30x2.65mm_HandSolder
R33, R34: 1.5k; R_1210_3225Metric_Pad1.30x2.65mm_HandSolder
RXD0: TestPoint; TestPoint_Pad_D2.0mm
SCL1: TestPoint; TestPoint_Pad_D2.0mm
SDA1: TestPoint; TestPoint_Pad_D2.0mm
SW5, SW6: boot_button; SW_Tactile_SPST_NO_Straight_CK_PTS636Sx25SMTRLFS; Manufacturer_Part_Number PTS636 SK25 SMTR LFS
TXD0: TestPoint; TestPoint_Pad_D2.0mm
U2: ESP32-WROOM-32
U3: CP2102-GMR; QFN28_5X5_SIL
U4: MPU-6050; InvenSense_QFN-24_4x4mm_P0.5mm

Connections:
3V3: 3V3.1, C1.1, C3.1, C9.1, C11.1, C12.1, R24.1, R25.2, R33.2, R34.2, U2.2 (VDD), U3.6 (VDD), U3.7 (REGIN), U4.8 (VLOGIC), U4.13 (VDD); also elsewhere on the board
5V: D5.1 (K); also elsewhere on the board
5V_USB: D5.2 (A), D7.2 (K_1), J6.A4 (VBUS_1), J6.A9 (VBUS_2), R26.1
ACC_SCL: R34.1, SCL1.1, U2.36 (IO22), U4.23 (SCL)
ACC_SDA: R33.1, SDA1.1, U2.33 (IO21), U4.24 (SDA)
BOOT: BOOT1.1, C13.1, Q4.3 (C), SW5.2, U2.25 (IO0)
BUTTON_CHANGE_LCD_PAGE: U2.14 (IO12); also elsewhere on the board
BUTTON_ON/OFF_VENTILATOR_STATUS: U2.37 (IO23); also elsewhere on the board
CAN_RX: U2.31 (IO19); also elsewhere on the board
CAN_TX: U2.12 (IO27); also elsewhere on the board
D+: D7.3 (K_2), J6.A6 (DP1), J6.B6 (DP2), U3.4 (D+)
D-: D7.4 (K_3), J6.A7 (DN1), J6.B7 (DN2), U3.5 (D-)
DTR: Q4.2 (E), R29.1, U3.28 (DTR)
EN: C10.1, EN1.1, Q3.3 (C), R24.2, SW6.2, U2.3 (EN)
GND: C1.2, C3.2, C9.2, C10.2, C11.2, C12.2, C13.2, C22.2, C23.2, D7.1 (COMMON_A), GND1.1, J6.A1 (GND_1), J6.A12 (GND_2), J6.MH3, J6.MH4, J6.MH5, J6.MH6, R22.2, R23.1, R27.2, SW5.1, SW6.1, U2.1 (GND), U2.15 (GND), U2.38 (GND), U2.39 (GND), U3.3 (GND), U3.29 (EPAD), U4.1 (CLKIN), U4.9 (AD0), U4.11 (FSYNC), U4.18 (GND); also elsewhere on the board
LED_NEUTRAL: U2.11 (IO26); also elsewhere on the board
LED_SHIFT: U2.10 (IO25); also elsewhere on the board
LED_STATUS: U2.8 (IO32); also elsewhere on the board
LED_STRIP: U2.9 (IO33); also elsewhere on the board
unnamed: J6.A5 (CC1), R23.2
unnamed: J6.B5 (CC2), R22.1
unnamed: Q3.1 (B), R29.2
unnamed: Q4.1 (B), R30.2
unnamed: R26.2, R27.1, U3.8 (VBUS)
unnamed: R25.1, U3.9 (~RST)
unnamed: C22.1, U4.20 (CPOUT)
unnamed: C23.1, U4.10 (REGOUT)
RSTD: U2.30 (IO18); also elsewhere on the board
RTS: Q3.2 (E), R30.1, U3.24 (RTS)
RXD: U2.28 (IO17); also elsewhere on the board
RXD0: RXD0.1, U2.34 (RXD0/IO3), U3.26 (TXD)
SC_STATUS: U2.7 (IO35); also elsewhere on the board
SD_CLK: U2.13 (IO14); also elsewhere on the board
SD_CS: U2.16 (IO13); also elsewhere on the board
SD_MISO: U2.26 (IO4); also elsewhere on the board
SD_MOSI: U2.23 (IO15); also elsewhere on the board
SWITCH_ROTARY_HYBRID: U2.6 (IO34); also elsewhere on the board
TXD: U2.27 (IO16); also elsewhere on the board
TXD0: TXD0.1, U2.35 (TXD0/IO1), U3.25 (RXD)

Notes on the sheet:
Auto programming circuit DTR RTS-->EN BOOT 1 1 1 1 0 0 1 1 1 0 0 1 0 1 1 0
C10 as debounce
ESP32_MODULE
ESD_PROTECTION
BUTTONS
must be pulled up during boot
USB-C 5V & USB-UART
thesis needed: ACC MPU6050
Reset Display signal
TEST_PINS
UART pins are inverted in firmware

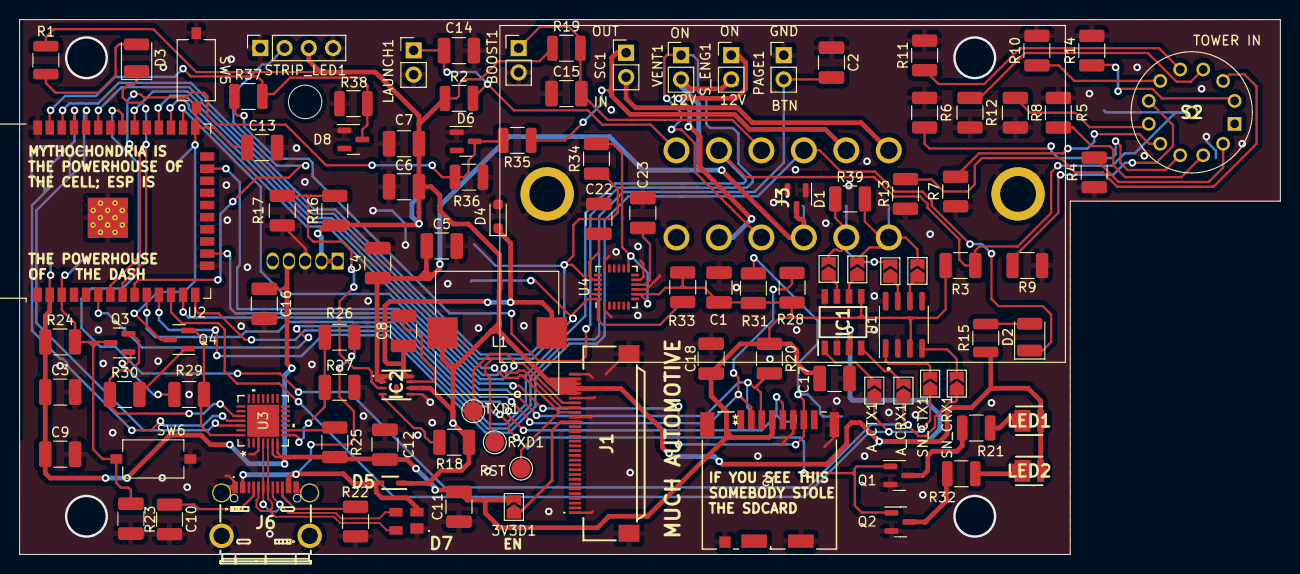
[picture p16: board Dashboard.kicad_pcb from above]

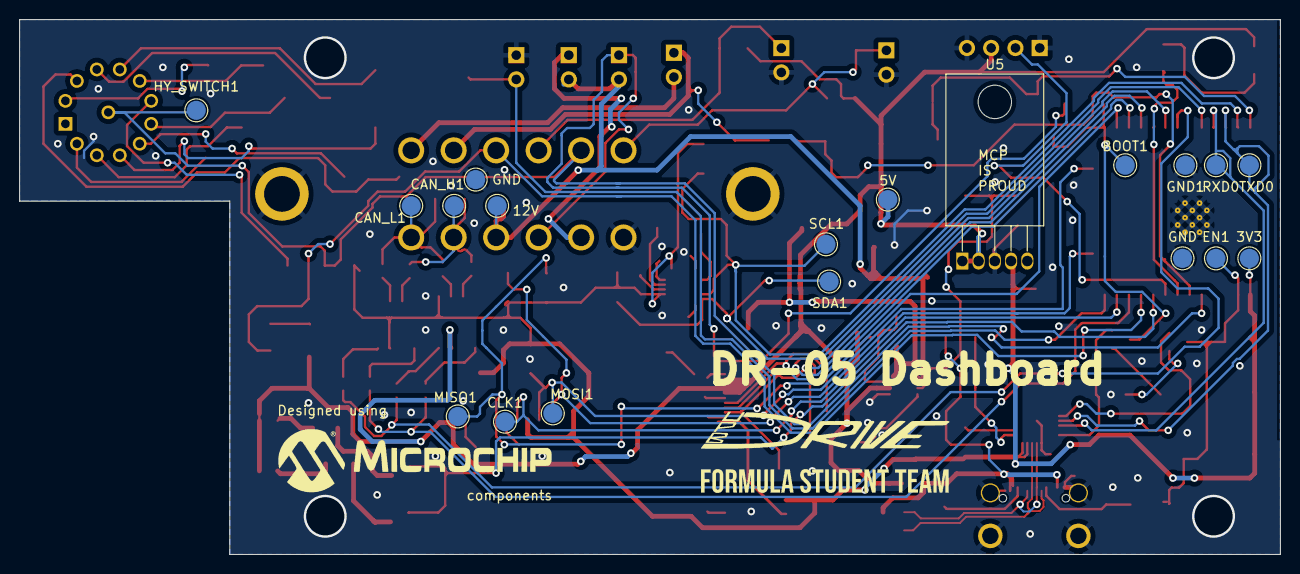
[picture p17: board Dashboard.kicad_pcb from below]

Board: 2 copper layers, 132.0 x 56.0 mm, 125 parts (19 on the bottom side), 78 nets.

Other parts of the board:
5V: TestPoint; TestPoint_Pad_D2.0mm
GND: TestPoint; TestPoint_Pad_D2.0mm
GND#2: TestPoint; TestPoint_Pad_D2.0mm
RST: TestPoint; TestPoint_Pad_D2.0mm

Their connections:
5V: 5V.1; also elsewhere on the board
GND: GND.1, GND#2.1; also elsewhere on the board
RSTD: RST.1; also elsewhere on the board

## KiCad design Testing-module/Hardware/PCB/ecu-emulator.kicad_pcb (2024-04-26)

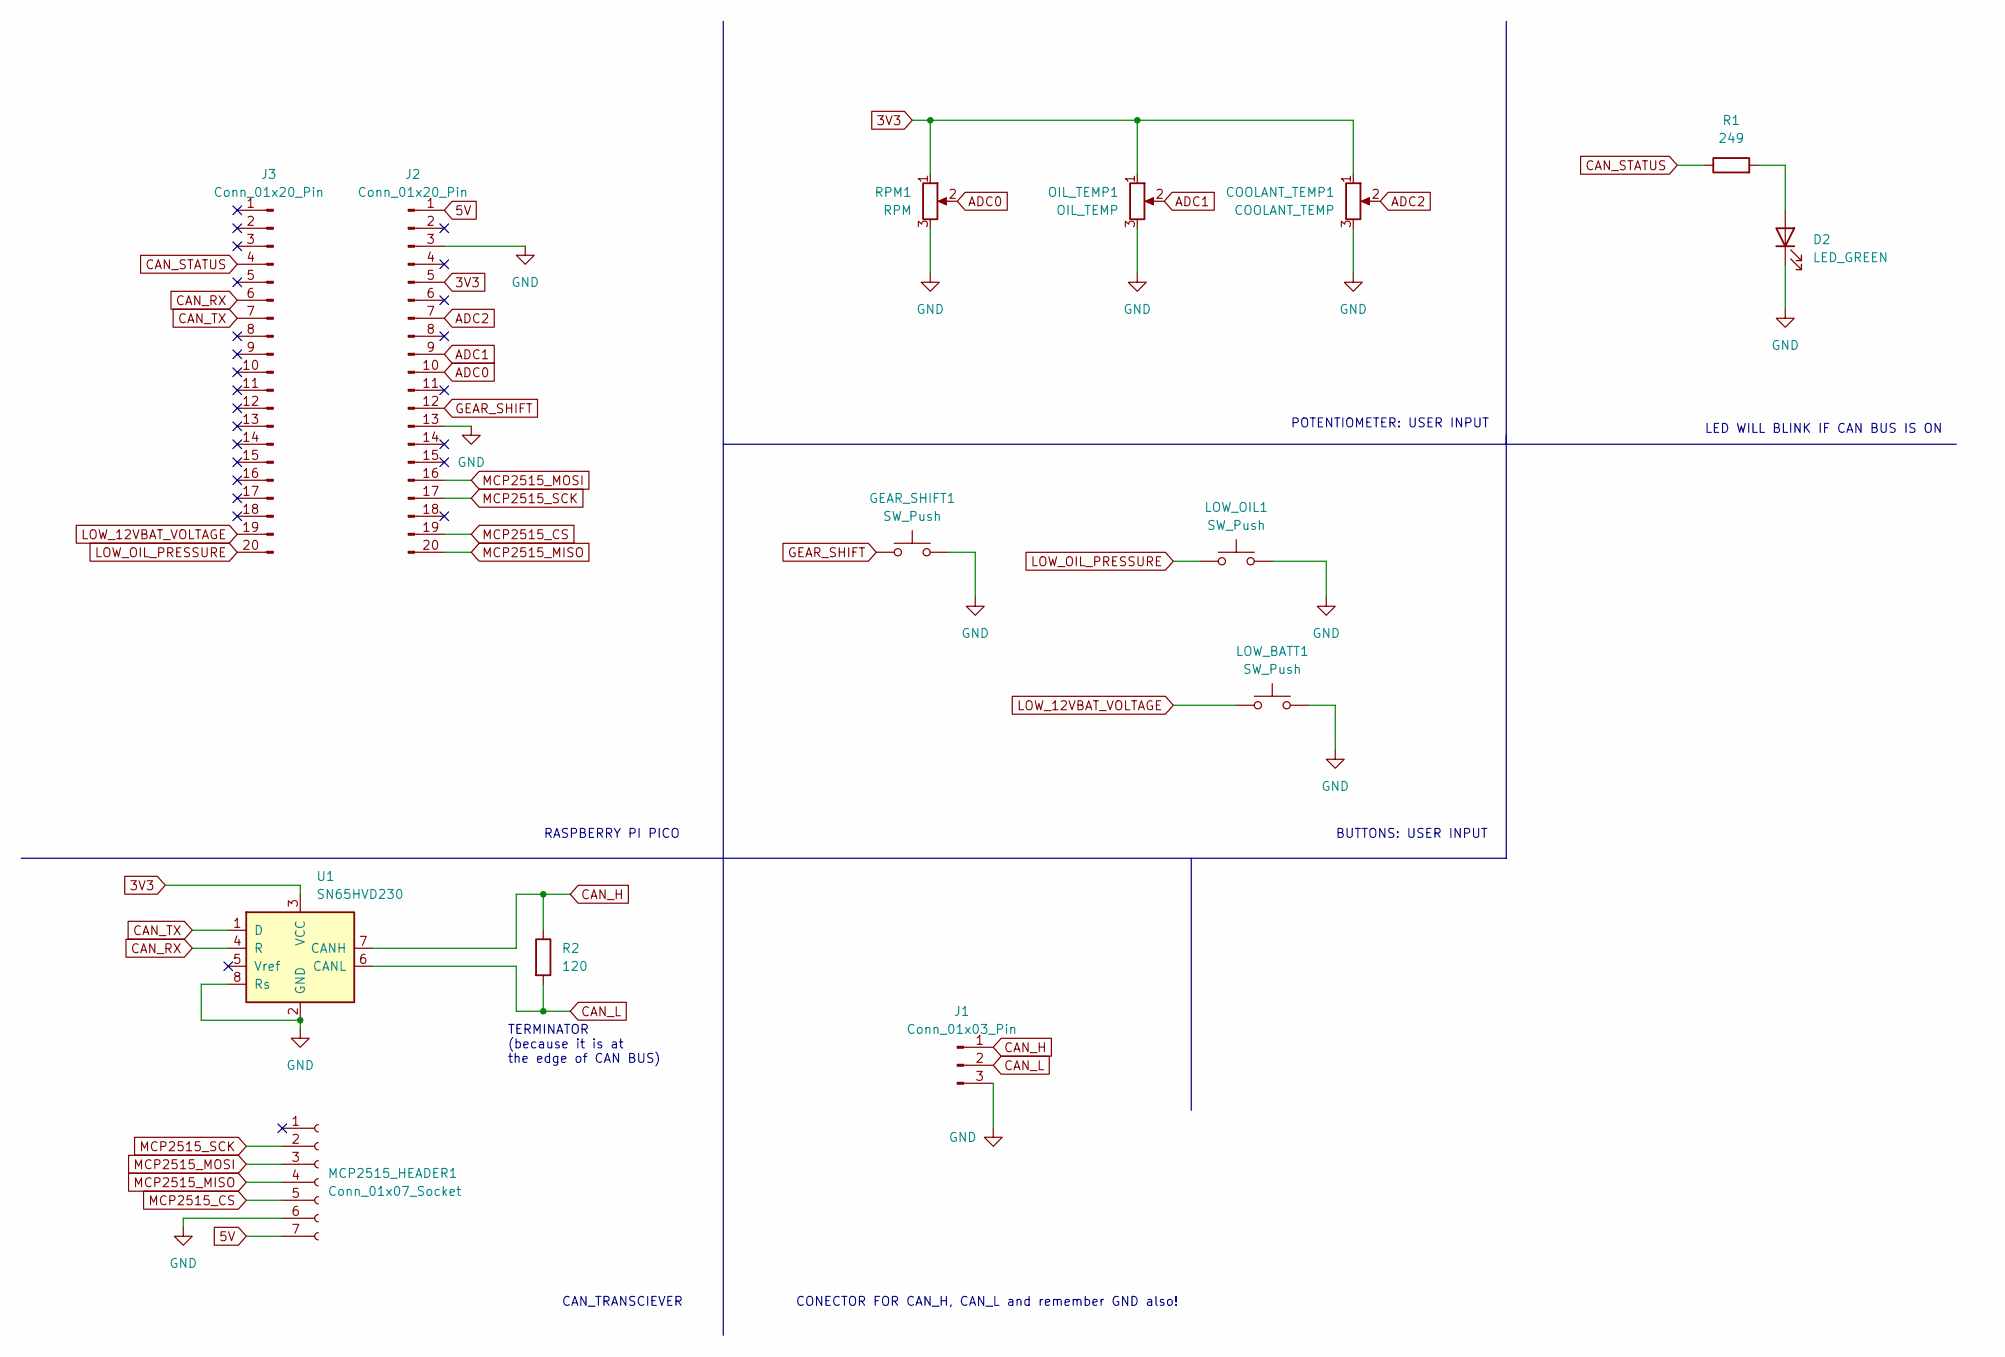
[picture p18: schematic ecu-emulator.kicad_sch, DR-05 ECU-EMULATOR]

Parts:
COOLANT_TEMP1: COOLANT_TEMP; Potentiometer_Alps_RK163_Single_Horizontal
D2: LED_GREEN; D_1210_3225Metric
GEAR_SHIFT1: SW_Push; SW_PUSH_6mm
J1: Conn_01x03_Pin; PinHeader_1x03_P2.54mm_Vertical
J2, J3: Conn_01x20_Pin; PinHeader_1x20_P2.54mm_Vertical
LOW_BATT1: SW_Push; SW_PUSH_6mm
LOW_OIL1: SW_Push; SW_PUSH_6mm
MCP2515_HEADER1: Conn_01x07_Socket; PinHeader_1x07_P2.54mm_Vertical
OIL_TEMP1: OIL_TEMP; Potentiometer_Alps_RK163_Single_Horizontal
R1: 249; R_1210_3225Metric_Pad1.30x2.65mm_HandSolder
R2: 120; R_1210_3225Metric_Pad1.30x2.65mm_HandSolder
RPM1: RPM; Potentiometer_Alps_RK163_Single_Horizontal
U1: SN65HVD230; SOIC-8_3.9x4.9mm_P1.27mm

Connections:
3V3: COOLANT_TEMP1.1, J2.5, OIL_TEMP1.1, RPM1.1, U1.3 (VCC)
5V: J2.1, MCP2515_HEADER1.7
ADC0: J2.10, RPM1.2
ADC1: J2.9, OIL_TEMP1.2
ADC2: COOLANT_TEMP1.2, J2.7
CAN_H: J1.1, R2.1, U1.7 (CANH)
CAN_L: J1.2, R2.2, U1.6 (CANL)
CAN_RX: J3.6, U1.4 (R)
CAN_STATUS: J3.4, R1.1
CAN_TX: J3.7, U1.1 (D)
GEAR_SHIFT: GEAR_SHIFT1.1, J2.12
GND: COOLANT_TEMP1.3, GEAR_SHIFT1.2, J1.3, J2.3, J2.13, LOW_BATT1.2, LOW_OIL1.2, MCP2515_HEADER1.6, OIL_TEMP1.3, RPM1.3, U1.2 (GND), U1.8 (Rs); also elsewhere on the board
LOW_12VBAT_VOLTAGE: J3.19, LOW_BATT1.1
LOW_OIL_PRESSURE: J3.20, LOW_OIL1.1
MCP2515_CS: J2.19, MCP2515_HEADER1.5
MCP2515_MISO: J2.20, MCP2515_HEADER1.4
MCP2515_MOSI: J2.16, MCP2515_HEADER1.3
MCP2515_SCK: J2.17, MCP2515_HEADER1.2
unnamed 18: R1.2; also elsewhere on the board

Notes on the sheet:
TERMINATOR (because it is at the edge of CAN BUS)
LED WILL BLINK IF CAN BUS IS ON
CAN_TRANSCIEVER
CONECTOR FOR CAN_H, CAN_L and remember GND also!
POTENTIOMETER: USER INPUT
RASPBERRY PI PICO
BUTTONS: USER INPUT

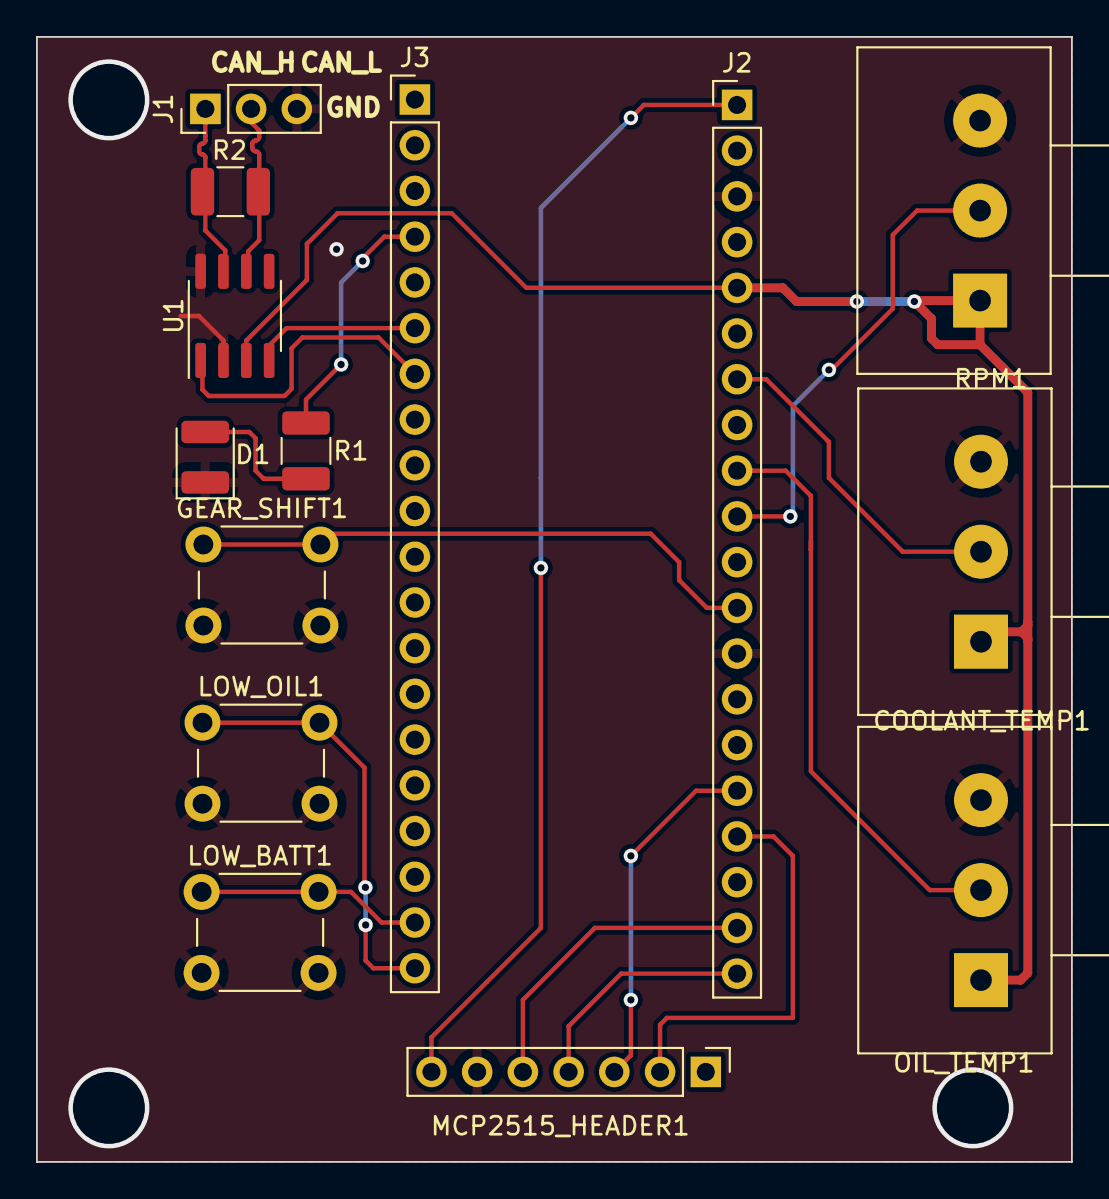
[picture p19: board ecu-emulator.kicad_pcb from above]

Board: 2 copper layers, 57.5 x 62.5 mm, 14 parts (0 on the bottom side), 19 nets.

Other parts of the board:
D1: LED_GREEN; D_1210_3225Metric

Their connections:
GND: D1.1 (K); also elsewhere on the board
unnamed 18: D1.2 (A); also elsewhere on the board

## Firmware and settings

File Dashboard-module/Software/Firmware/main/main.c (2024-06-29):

/******************************************************************************/
/* UPBDRIVE Dashboard Firmware                                                */
/* All rights reserverd 2023                                                  */
/******************************************************************************/

/* Include tasks */
#include <lcd_task.h>
#include <led_task.h>
#include <heartbeat_task.h>
#include <can_task.h>
#include <accelerometer_task.h>
#include <hybrid_selector_task.h>
#include <sdcard_task.h>
#include <buttons_task.h>
#include <wifi_task.h>
#include <timer_task.h>

#include <common.h>
#include <stdio.h>
#include <driver/gpio.h>
#include <freertos/FreeRTOS.h>
#include <freertos/task.h>

////////////////////////////////////////////////////////////////////////////////
////                       GLOBAL VARIABLES                                 ////
////////////////////////////////////////////////////////////////////////////////

/* Global semaphore for display_data struct */
SemaphoreHandle_t xSemaphore_display_data;

display_data_t display_data =
{
    /* Initialize the structure members with 0 */
    0
};

status_firmware_t general_status =
{
    /* Initialize the structure members with 0 */
    0
};

////////////////////////////////////////////////////////////////////////////////
////                       GLOBAL FUNCTIONS                                 ////
////////////////////////////////////////////////////////////////////////////////

////////////////////////////////////////////////////////////////////////////////
////                       LOCAL MACROS                                     ////
////////////////////////////////////////////////////////////////////////////////

////////////////////////////////////////////////////////////////////////////////
////                       LOCAL CONSTANTS                                  ////
////////////////////////////////////////////////////////////////////////////////

////////////////////////////////////////////////////////////////////////////////
////                       LOCAL FUNCTIONS                                 ////
////////////////////////////////////////////////////////////////////////////////

esp_err_t dashboard_init()
{
    esp_err_t esp_response                    = ESP_FAIL;
    twai_mode_t can_mode                      = TWAI_MODE_NORMAL;
    #if (CAN_SPEED == 250)
    twai_timing_config_t can_speed            = TWAI_TIMING_CONFIG_250KBITS();
    #elif (CAN_SPEED == 500)
    twai_timing_config_t can_speed            = {.clk_src = TWAI_CLK_SRC_APB, .quanta_resolution_hz = 8000000, .brp = 10, .tseg_1 = 13, .tseg_2 = 2, .sjw = 1, .triple_sampling = false};
    #elif (CAN_SPEED == 800)
    twai_timing_config_t can_speed            = TWAI_TIMING_CONFIG_800KBITS();
    #elif (CAN_SPEED == 1000)
    twai_timing_config_t can_speed            = TWAI_TIMING_CONFIG_1MBITS();
    #endif /* CAN_SPEED */
    twai_filter_config_t packet_filter_config = TWAI_FILTER_CONFIG_ACCEPT_ALL();

    general_status.display_data               = &display_data;
    general_status.time_second                = 99U;
    general_status.time_minute                = 99U;
    general_status.time_hour                  = 99U;
    general_status.sdcard_logging             = false;

    /* setup the lcd display */
    ESP_ERROR_CHECK(lcd_setup());

    /* setup can bus */
    ESP_ERROR_CHECK(can_setup(can_mode, &can_speed, &packet_filter_config));

    /* setup buttons */
    ESP_ERROR_CHECK(buttons_setup());

    /* setup led status */
    ESP_ERROR_CHECK(heartbeat_setup());

    /* setup the Semaphore for display data */
    xSemaphore_display_data                = xSemaphoreCreateBinary();
    general_status.xSemaphore_display_data = xSemaphore_display_data;

    /* Because for some reason it is initialized to 0 instead of 1*/
    xSemaphoreGive(xSemaphore_display_data);

    /* Init RTC data in general_status with 99 which is an imposible value */

    /* setup the shift and neutral led */
    ESP_ERROR_CHECK(shift_neutral_led_setup());

    /* setup shift strip */
    ESP_ERROR_CHECK(shift_strip_led_setup());

    /* setup the accelerometer module */
    ESP_ERROR_CHECK(accelerometer_setup());

    /* setup the hybrid selector */
    ESP_ERROR_CHECK(hybrid_selector_setup());

    /* setup the sdcard module */
    ESP_ERROR_CHECK(sdcard_setup());

    /* setup wifi */
    wifi_setup();

    /* setup http server */
    ESP_ERROR_CHECK(http_server_setup());

    /* ToDo override time check */
    general_status.time_second = 0;
    general_status.time_minute = 30;
    general_status.time_hour   = 12;

    /* setup timer for data logging - every second increments the time value
       stored in general_status struct */
    ESP_ERROR_CHECK(timer_setup());

    esp_response = ESP_OK;
    return esp_response;
}


void app_main(void)
{
    esp_err_t esp_response = ESP_FAIL;
    esp_response = dashboard_init();

    if (esp_response != ESP_OK)
    {
        while(true)
        {
            printf("Dashboard failed to initialize\n");
            vTaskDelay(1000 / portTICK_PERIOD_MS);
            /* Infinite loop caused by dash perpiherals
                init failure */
        }
    }

    /* CORE 0 tasks*/
    xTaskCreatePinnedToCore(heartbeat,            "heartbeat",            1024, NULL,                             0, NULL, 0);
    xTaskCreatePinnedToCore(can_read,             "can_read",             2048, &general_status,                  3, NULL, 0);
    xTaskCreatePinnedToCore(can_send,             "can_send",             2048, &general_status,                  3, NULL, 0);
    xTaskCreatePinnedToCore(accelerometer_read,   "accelerometer_read",   2048, &general_status,                  1, NULL, 0);
    xTaskCreatePinnedToCore(hybrid_selector_read, "hybrid_selector_read", 2048, &general_status,                  2, NULL, 0);

    /* CORE 1 tasks */
    xTaskCreatePinnedToCore(neutral_led_update,       "shift_neutral_led_update",   1024, &general_status,                  0, NULL, 1);
    xTaskCreatePinnedToCore(shift_strip_led_update,   "shift_strip_led_update",     4096, &general_status,                  1, NULL, 1);
    xTaskCreatePinnedToCore(lcd_update,               "lcd_update",                 4096, &general_status,                  3, NULL, 1);
    xTaskCreatePinnedToCore(sdcard_write,             "sdcard_write",               4096, &general_status,                  2, NULL, 1);

    /* DEBUG tasks */
    #ifdef ENABLE_DEBUG_BUTTONS
    xTaskCreatePinnedToCore(buttons_read,         "buttons_task",         1024, NULL,                             0, NULL, 0);
    #endif /* ENABLE_DEBUG_BUTTONS */

}

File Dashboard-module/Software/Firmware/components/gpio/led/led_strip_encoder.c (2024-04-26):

/*
 * SPDX-FileCopyrightText: 2021-2022 Espressif Systems (Shanghai) CO LTD
 *
 * SPDX-License-Identifier: Apache-2.0
 */

#include <esp_check.h>
#include <led_strip_encoder.h>

static const char *TAG = "led_encoder";
typedef struct {
    rmt_encoder_t base;
    rmt_encoder_t *bytes_encoder;
    rmt_encoder_t *copy_encoder;
    int state;
    rmt_symbol_word_t reset_code;
} rmt_led_strip_encoder_t;

rmt_led_strip_encoder_t led_encoder = {0};

static size_t rmt_encode_led_strip(rmt_encoder_t *encoder, rmt_channel_handle_t channel, const void *primary_data, size_t data_size, rmt_encode_state_t *ret_state)
{
    rmt_led_strip_encoder_t *led_encoder = __containerof(encoder, rmt_led_strip_encoder_t, base);
    rmt_encoder_handle_t bytes_encoder = led_encoder->bytes_encoder;
    rmt_encoder_handle_t copy_encoder = led_encoder->copy_encoder;
    rmt_encode_state_t session_state = RMT_ENCODING_RESET;
    rmt_encode_state_t state = RMT_ENCODING_RESET;
    size_t encoded_symbols = 0;
    switch (led_encoder->state) {
    case 0: // send RGB data
        encoded_symbols += bytes_encoder->encode(bytes_encoder, channel, primary_data, data_size, &session_state);
        if (session_state & RMT_ENCODING_COMPLETE) {
            led_encoder->state = 1; // switch to next state when current encoding session finished
        }
        if (session_state & RMT_ENCODING_MEM_FULL) {
            state |= RMT_ENCODING_MEM_FULL;
            goto out; // yield if there's no free space for encoding artifacts
        }
    // fall-through
    case 1: // send reset code
        encoded_symbols += copy_encoder->encode(copy_encoder, channel, &led_encoder->reset_code,
                                                sizeof(led_encoder->reset_code), &session_state);
        if (session_state & RMT_ENCODING_COMPLETE) {
            led_encoder->state = RMT_ENCODING_RESET; // back to the initial encoding session
            state |= RMT_ENCODING_COMPLETE;
        }
        if (session_state & RMT_ENCODING_MEM_FULL) {
            state |= RMT_ENCODING_MEM_FULL;
            goto out; // yield if there's no free space for encoding artifacts
        }
    }
out:
    *ret_state = state;
    return encoded_symbols;
}

static esp_err_t rmt_del_led_strip_encoder(rmt_encoder_t *encoder)
{
    rmt_led_strip_encoder_t *led_encoder = __containerof(encoder, rmt_led_strip_encoder_t, base);
    rmt_del_encoder(led_encoder->bytes_encoder);
    rmt_del_encoder(led_encoder->copy_encoder);
    free(led_encoder);
    return ESP_OK;
}

static esp_err_t rmt_led_strip_encoder_reset(rmt_encoder_t *encoder)
{
    rmt_led_strip_encoder_t *led_encoder = __containerof(encoder, rmt_led_strip_encoder_t, base);
    rmt_encoder_reset(led_encoder->bytes_encoder);
    rmt_encoder_reset(led_encoder->copy_encoder);
    led_encoder->state = RMT_ENCODING_RESET;
    return ESP_OK;
}

esp_err_t rmt_new_led_strip_encoder(const led_strip_encoder_config_t *config, rmt_encoder_handle_t *ret_encoder)
{
    esp_err_t ret = ESP_OK;

    ESP_GOTO_ON_FALSE(config && ret_encoder, ESP_ERR_INVALID_ARG, err, TAG, "invalid argument");
    led_encoder.base.encode = rmt_encode_led_strip;
    led_encoder.base.del = rmt_del_led_strip_encoder;
    led_encoder.base.reset = rmt_led_strip_encoder_reset;
    // different led strip might have its own timing requirements, following parameter is for WS2812
    rmt_bytes_encoder_config_t bytes_encoder_config = {
        .bit0 = {
            .level0 = 1,
            .duration0 = 0.3 * config->resolution / 1000000, // T0H=0.3us
            .level1 = 0,
            .duration1 = 0.9 * config->resolution / 1000000, // T0L=0.9us
        },
        .bit1 = {
            .level0 = 1,
            .duration0 = 0.9 * config->resolution / 1000000, // T1H=0.9us
            .level1 = 0,
            .duration1 = 0.3 * config->resolution / 1000000, // T1L=0.3us
        },
        .flags.msb_first = 1 // WS2812 transfer bit order: G7...G0R7...R0B7...B0
    };
    ESP_GOTO_ON_ERROR(rmt_new_bytes_encoder(&bytes_encoder_config, &led_encoder.bytes_encoder), err, TAG, "create bytes encoder failed");
    rmt_copy_encoder_config_t copy_encoder_config = {};
    ESP_GOTO_ON_ERROR(rmt_new_copy_encoder(&copy_encoder_config, &led_encoder.copy_encoder), err, TAG, "create copy encoder failed");

    uint32_t reset_ticks = config->resolution / 1000000 * 50 / 2; // reset code duration defaults to 50us
    led_encoder.reset_code = (rmt_symbol_word_t) {
        .level0 = 0,
        .duration0 = reset_ticks,
        .level1 = 0,
        .duration1 = reset_ticks,
    };
    *ret_encoder = &led_encoder.base;
    return ESP_OK;
err:
    return ret;
}

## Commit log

2024-04-26 Initial commit
    Signed-off: tudor.marculescu@stud.etti.upb.ro
    [4dsys.cfg, BOM.csv, Dashboard.kicad_pcb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]
2024-06-29 feature: Add latest docs
    [Dashboard.kicad_sch, esp32-integration.kicad_sch]
